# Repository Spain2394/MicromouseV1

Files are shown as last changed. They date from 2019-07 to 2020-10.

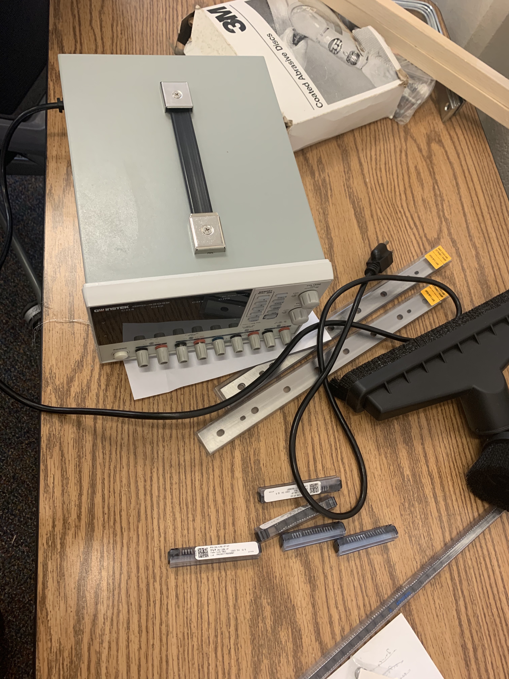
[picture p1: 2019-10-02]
docs/Notes/Electronics Notes/powersupplyy-return.jpg

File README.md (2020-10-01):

# Introduction
Micromouse (small robot car) PCB, boards are  designed in [EAGLE](http://eagle.autodesk.com)

Current board release [micromouse_board_revB_V0.0.16_2020-02-19.zip ](https://github.com/uga-robotics/MicromouseV1/blob/master/micromouse-main-board/micromouse-revB/micromouse_board_revB_V0.0.16_2020-02-19.zip ). Inside this zip file you will CAM files for assembly and manufacturing. 
Board BOM  --> [micromouse_board_revB_V0.0.16_2020-02-19.xlsx](https://github.com/uga-robotics/MicromouseV1/blob/master/micromouse-main-board/micromouse-revB/micromouse_board_revB_V0.0.16.xlsx)

## Getting going
Clone to hardware of software to local machine: ```git clone --recurse-submodules https://github.com/uga-robotics/MicromouseV1.git```

# Table of contents
1. [Bill Of Materials](https://github.com/Spain2394/MicromouseV1/blob/master/Wiki/Bill-of-Materials.md)
2. [Hardware Setup](https://github.com/Spain2394/MicromouseV1/blob/master/Wiki/Hardware-Setup.md)
3. [Software Setup](https://github.com/Spain2394/MicromouseV1/blob/master/Wiki/Software-Setup.md)

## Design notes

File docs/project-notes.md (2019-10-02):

# Project Notes:
### Resources
- [Futura robot information](http://micromouseusa.com/?page_id=1342)
- [Micromouse educational slides](http://micromouseusa.com/?page_id=1342)
- [Design Template: IEEE Micromouse Green Giant](http://greenye.net/Pages/Micromouse/Micromouse2012-2013.htm)
- [Design Template by: etank7000/Micromouse](https://github.com/etank7000/Micromouse)
- [Choosing IR Sensors](http://www.micromouseonline.com/2015/11/03/zeetah-sensor-design/)
- [Choosing a Motor](http://www.micromouseonline.com/2015/11/03/zeetah-sensor-design/)

### For Micromouse presentation slides see UCLA [notes](http://micromouse.ieeebruins.org/index.php/Main_Pages)

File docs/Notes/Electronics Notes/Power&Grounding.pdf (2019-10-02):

POWER AND GROUNDING

Dennis M. Briggs

Continuing Lecturer, UCLA Department of Electrical Engineering

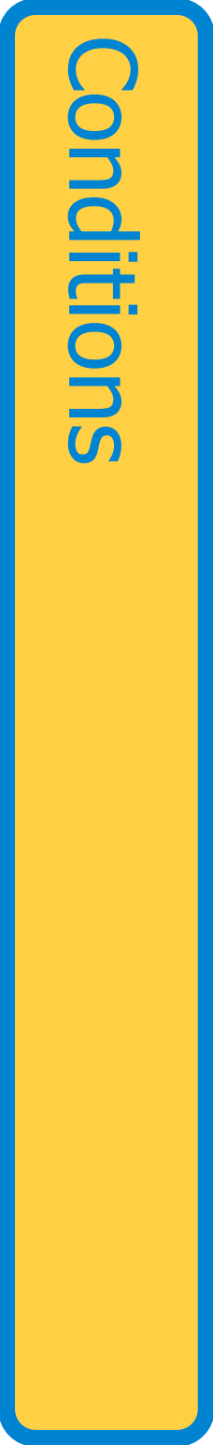
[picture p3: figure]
Conditions

- You will have one battery (OK, 2 for 7.4V)
- But you need different voltages
- + 5V0 for sensors
- +3V3 for microcontroller
- ± 5-7 V to drive motor control MOSFETS
- DC-to-DC converters can do these things

●
You will have one battery (OK, 2 for 7.4V)
- But you need different voltages
- + 5V0 for sensors
- +3V3 for microcontroller
- ± 5-7 V to drive motor control MOSFETS
- DC-to-DC converters can do these things

●
Charge Pumps
- High voltage, low current
- OK for driving MOSFETs
- Linear Regulators
- Simple
- Low noise
- Not efficient if big drop
- Standard andLow Dropout (LDO)
- Switching Regulators
- Efficient
- High noise
- Non-inverting & inverting
- Boost, Buck,and Buck-Boost

●
Charge Pumps
- High voltage, low current
- OK for driving MOSFETs
- Linear Regulators
- Simple
- Low noise
- Not efficient if big drop
- Standard andLow Dropout (LDO)
- Switching Regulators
- Efficient
- High noise
- Non-inverting & inverting
- Boost, Buck,and Buck-Boost

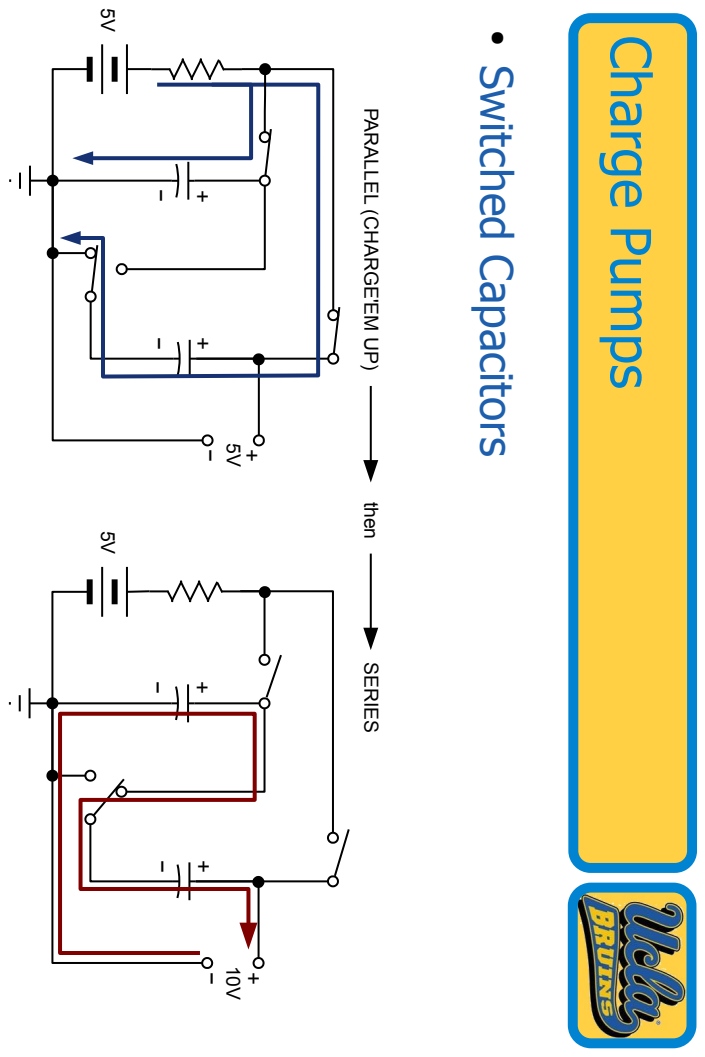
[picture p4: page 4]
● Switched Capacitors; Charge Pumps; then

PARALLEL (CHARGE'EM UP) SERIES

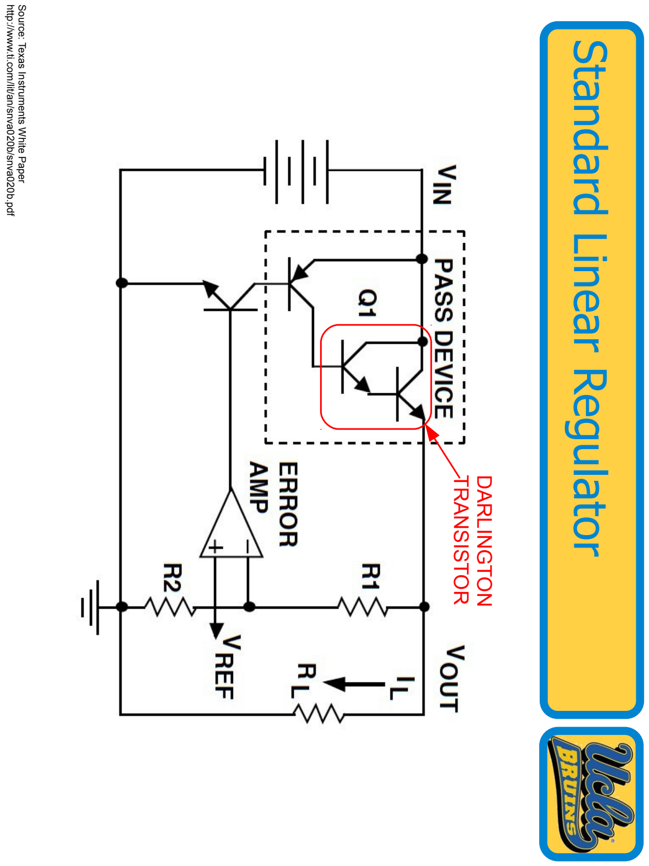
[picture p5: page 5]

Standard Linear Regulator

http://www.ti.com/lit/an/snva020b/snva020b.pdf

Source: Texas Instruments White Paper

TRANSISTOR

DARLINGTON

Standard Linear Regulator

http://www.ti.com/lit/an/snva020b/snva020b.pdf

Source: Texas Instruments White Paper

TRANSISTOR

DARLINGTON

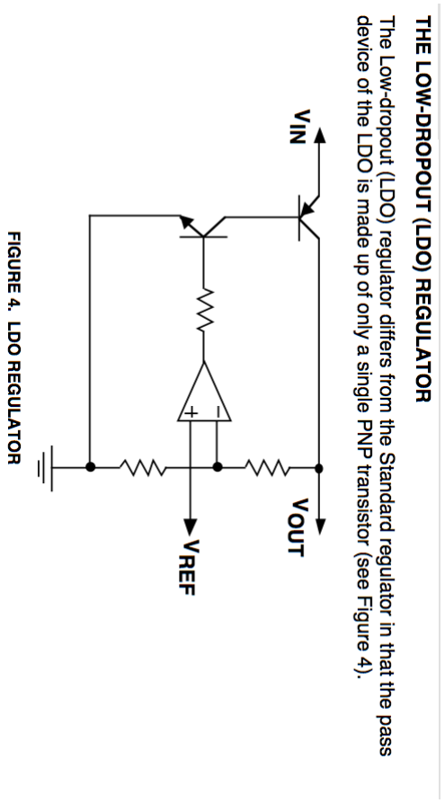
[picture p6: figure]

http://www.ti.com/lit/an/snva020b/snva020b.pdf

Source: Texas Instruments White Paper

v

n =

V REF

=

V OUT R2

R1

R2 V OUT

=
V REF

R1

R2

R2

=
V REF 1

R1

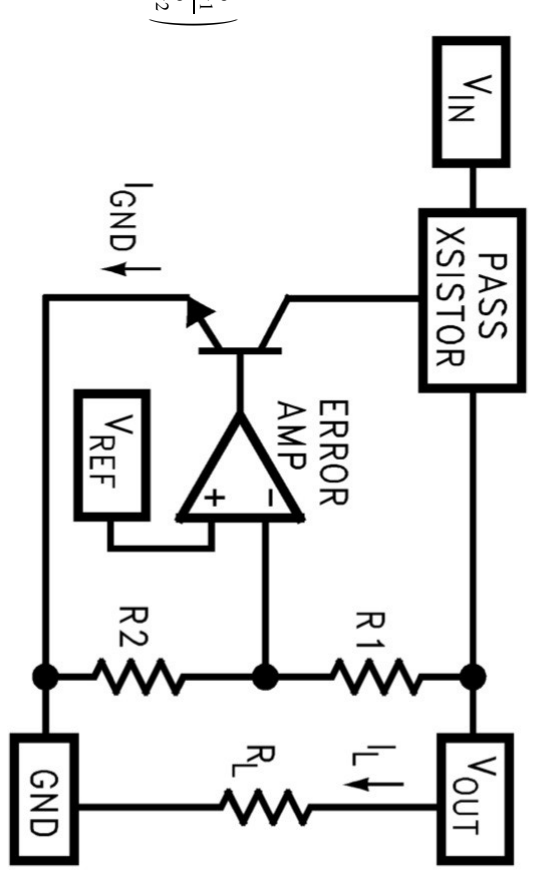
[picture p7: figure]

R2

holds.

summing point constraint

Negative feedback;

http://www.ti.com/lit/an/snva020b/snva020b.pdf

Source: Texas Instruments White Paper

v

n =

V REF

=

V OUT R2

R1

R2 V OUT

=
V REF

R1

R2

R2

=
V REF 1

R1

R2

holds.

summing point constraint

Negative feedback;

http://www.ti.com/lit/an/snva020b/snva020b.pdf

Source: Texas Instruments White Paper

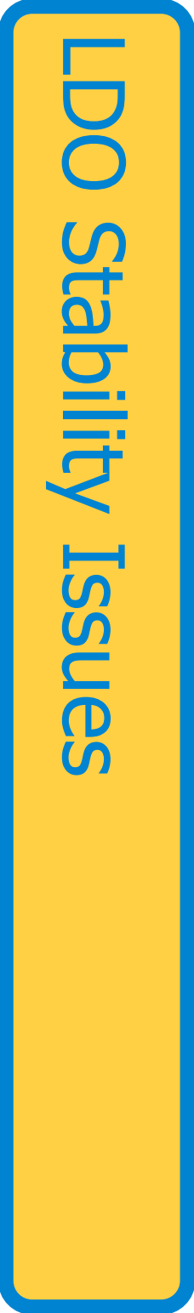
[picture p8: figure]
LDO Stability Issues

source: http://www.ti.com/lit/an/snva020b/snva020b.pdf

Source: Micrel MIC39000/39001/39002 Data sheet Source: Micrel MIC39000/39001/39002 Data sheet

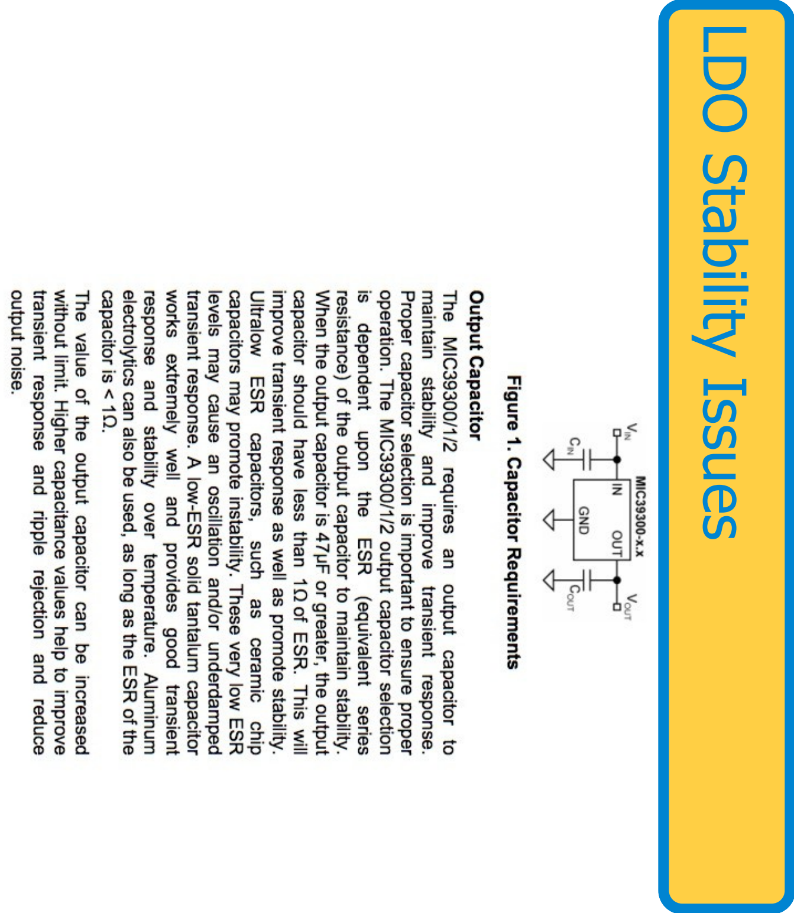
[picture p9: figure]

Stability Issues LDO Stability Issues Stability Issues LDO Stability Issues

http://www.national.com/assets/en/appnotes/f4.pdf

Source: National Semiconductor White Paper

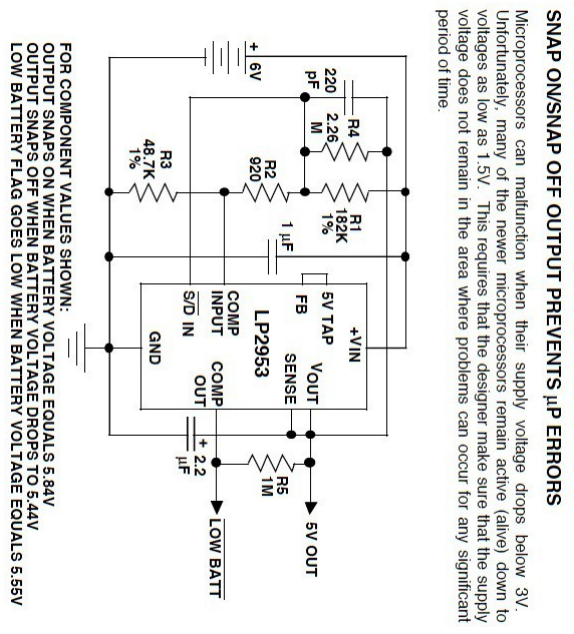
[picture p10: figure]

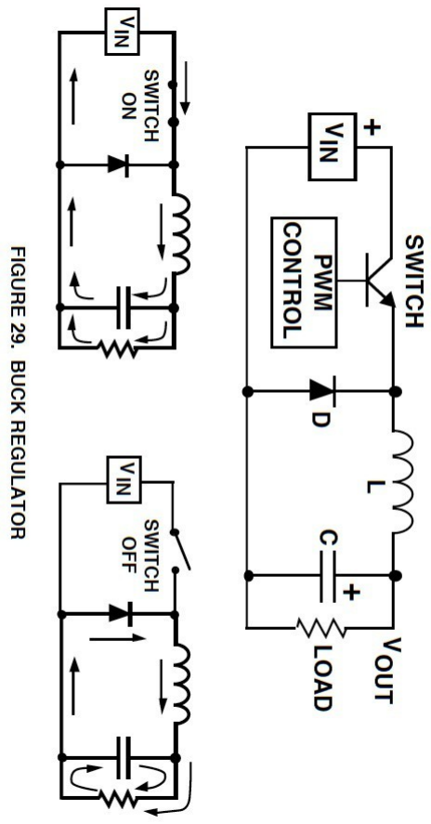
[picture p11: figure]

http://www.national.com/assets/en/appnotes/f5.pdf

Source: National Semiconductor White Paper

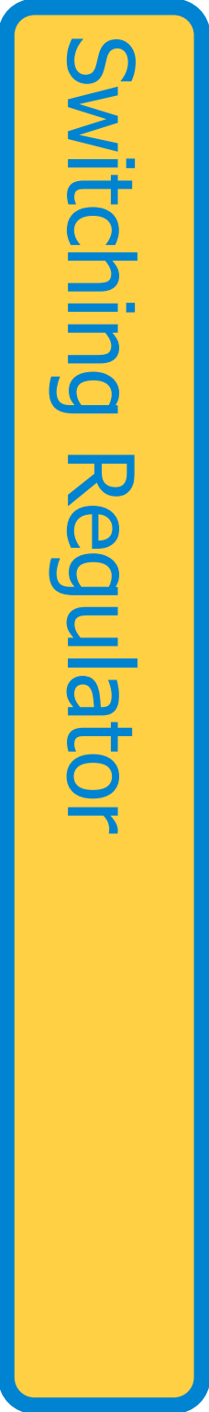
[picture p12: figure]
Switching Regulator

Source: Maxim Appnotes

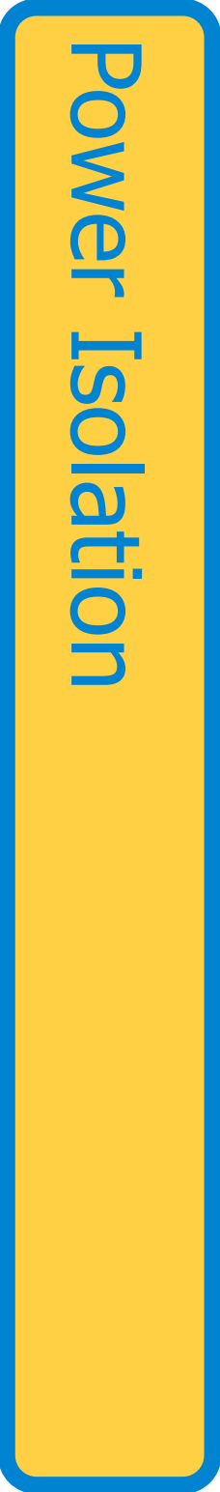
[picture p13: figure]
Power Isolation

Source: Prof. Richard Spencer, UCD

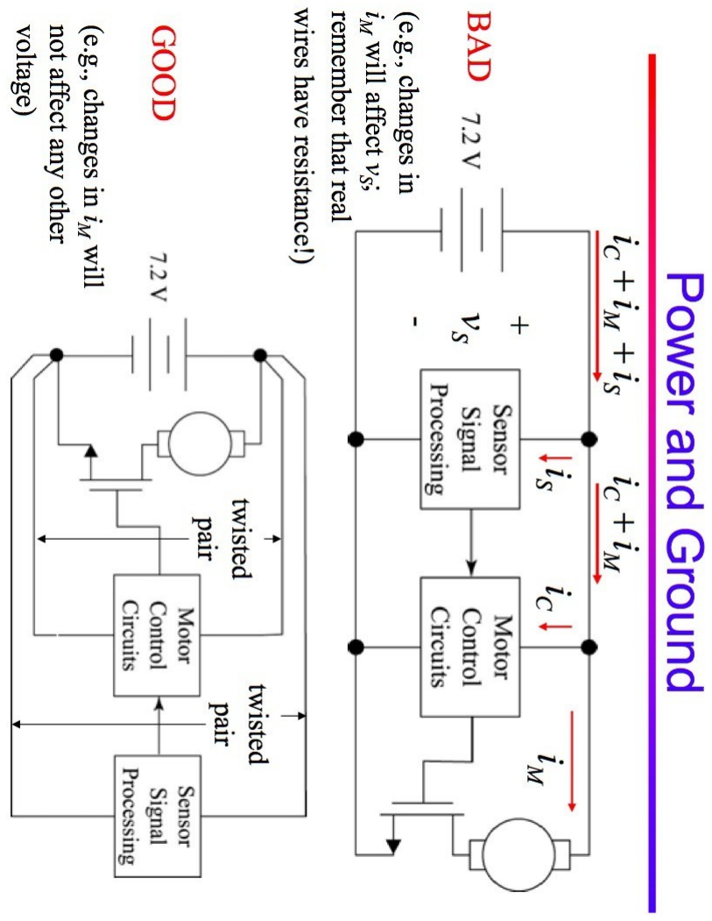
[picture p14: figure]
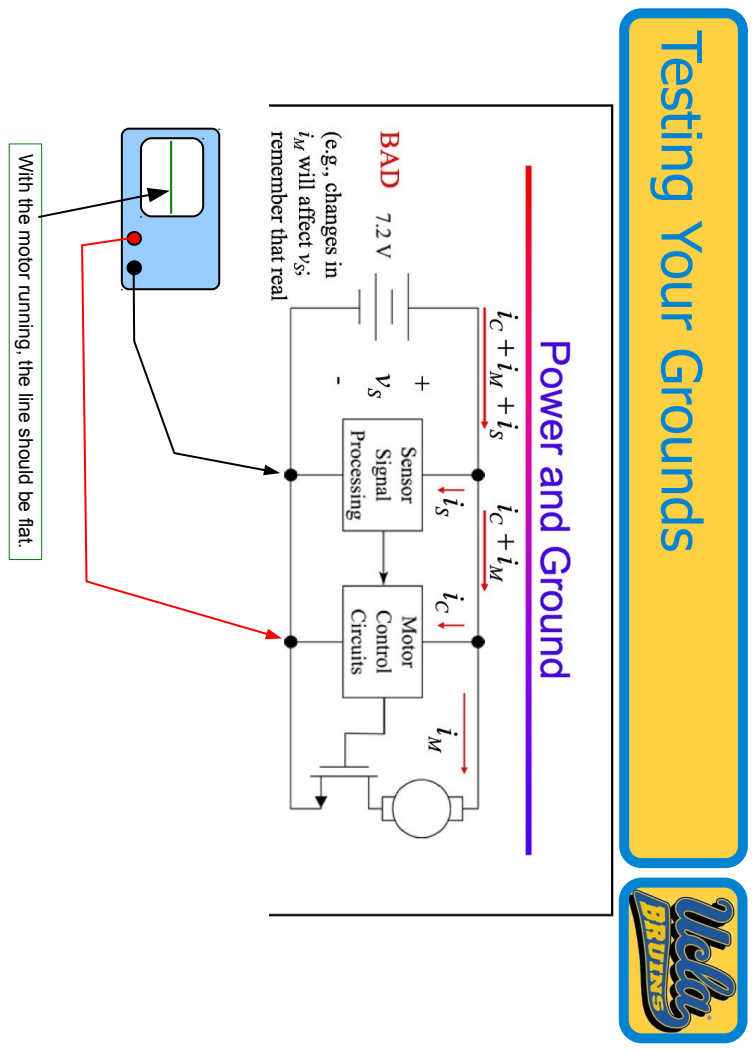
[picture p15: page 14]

Testing Your Grounds

With the motor running, the line should be flat.

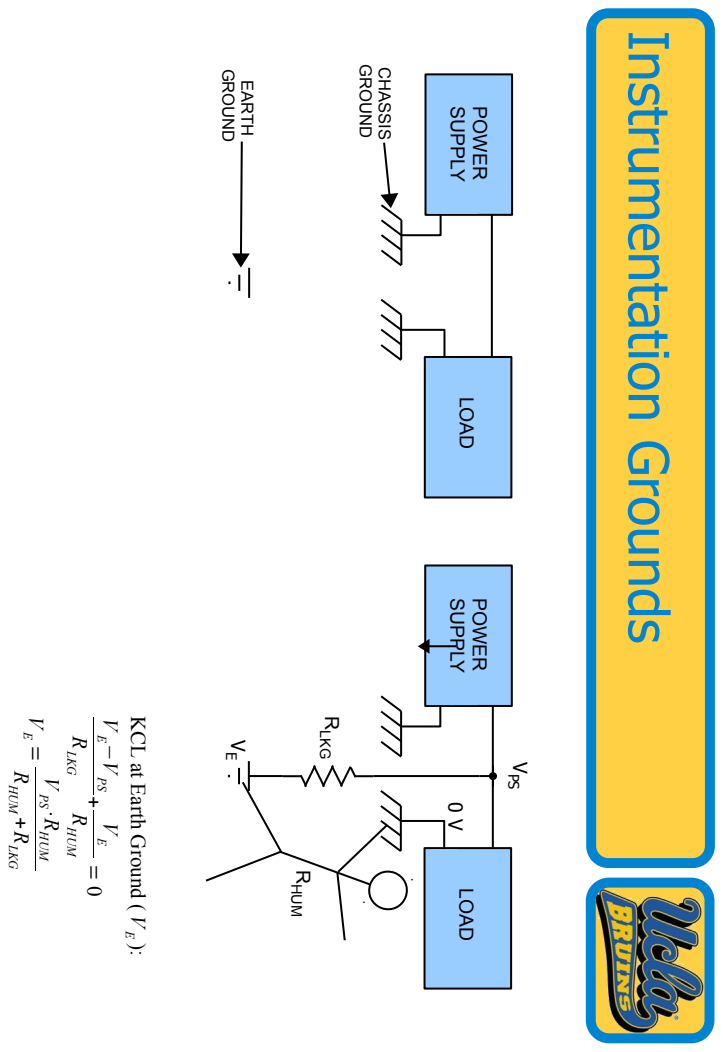
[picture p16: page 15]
Instrumentation Grounds; SUPPLY; GROUND; CHASSIS; EARTH; RLKG; RHUM; E − VPS; E = V PS⋅RHUM; + RLKG; VPS

POWER LOAD SUPPLY POWER LOAD

KCL at Earth Ground (

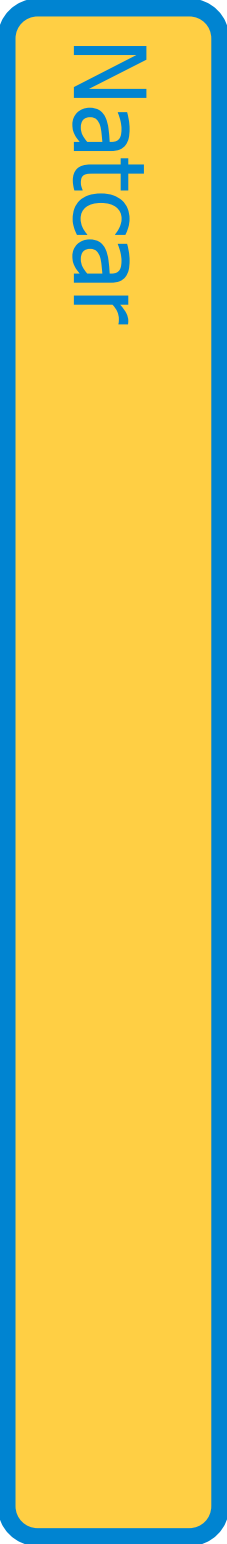
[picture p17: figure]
Natcar

A NATCAR GROUNDING STORY

Source: “NATCAR – Team Pathfinder”; John J. Jang, Siu Ching (Connie) Kwan, Sonny T. Bui, Michael

Chan, UCLA Department of Electrical Engineering, Final Report, Course EE184D, 2012-13 School Year

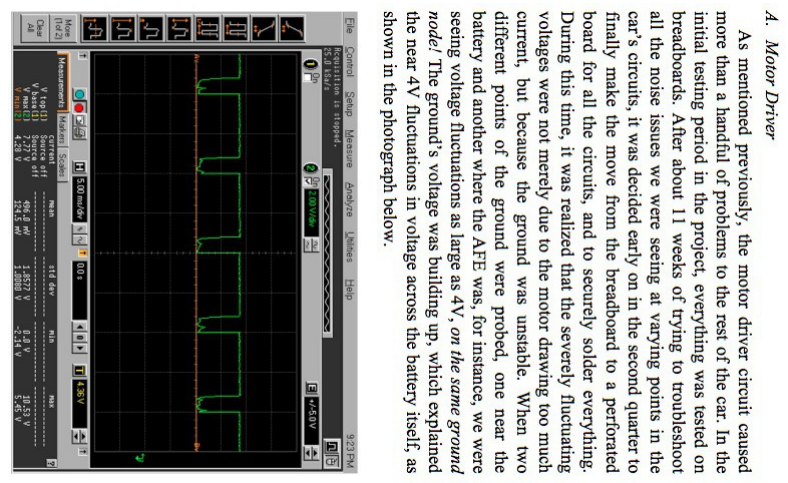
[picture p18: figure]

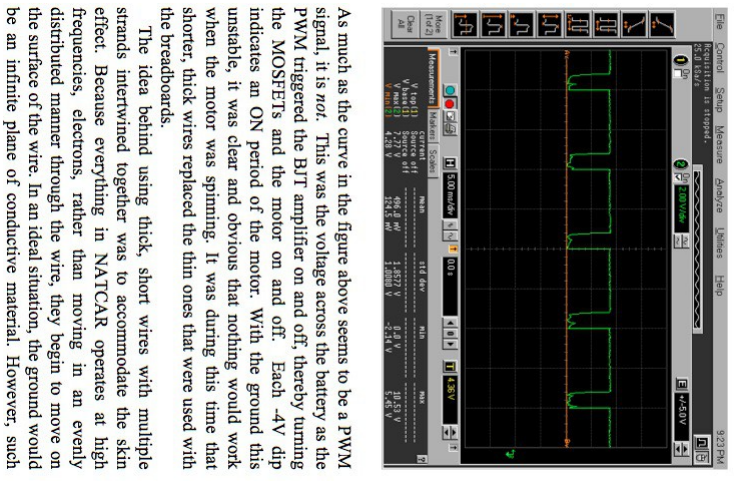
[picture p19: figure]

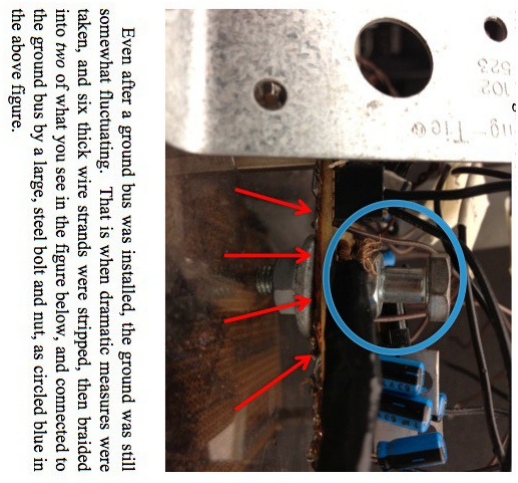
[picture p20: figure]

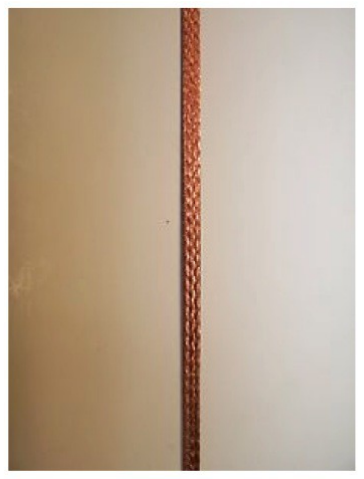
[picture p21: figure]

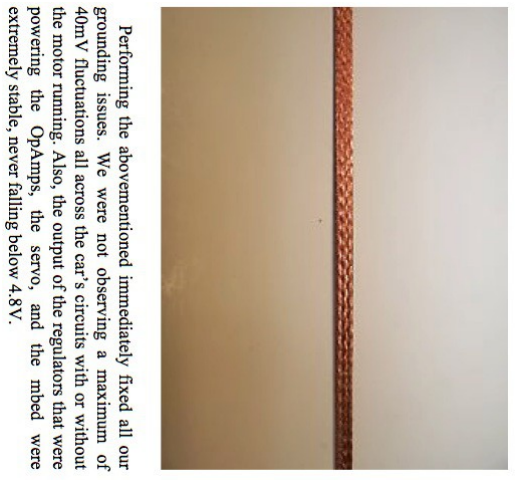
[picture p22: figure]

Power Isolation

Source: Prof. Richard Spencer, UCD

1/4-20 BOLT

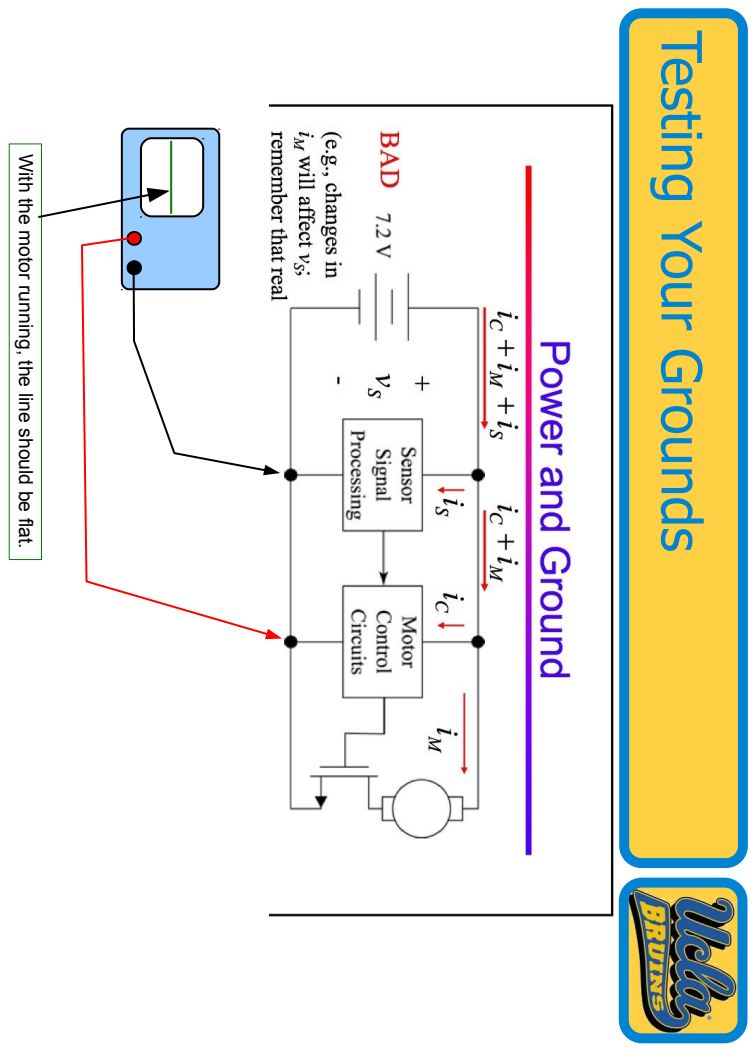
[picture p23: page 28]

Testing Your Grounds

With the motor running, the line should be flat.

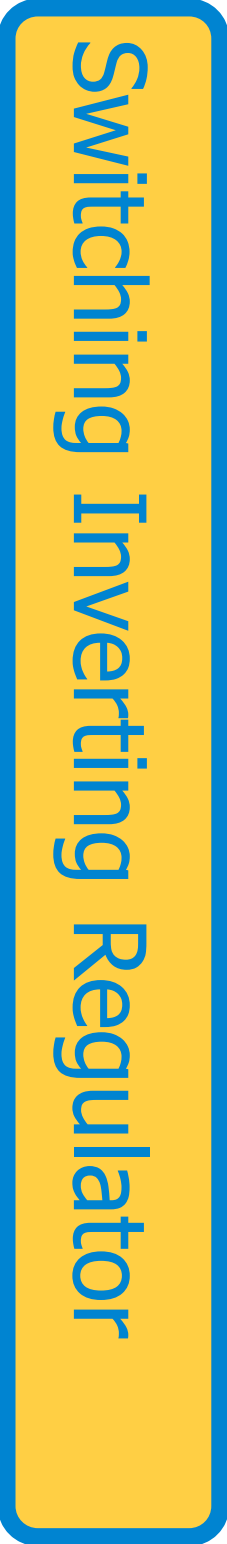
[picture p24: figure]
Switching Inverting Regulator

http://www.national.com/assets/en/appnotes/f5.pdf

Source: National Semiconductor White Paper

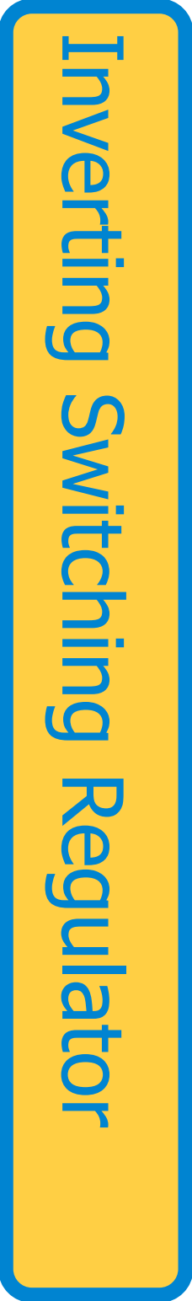
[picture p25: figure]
Inverting Switching Regulator

Source: Prof. Richard Spencer, UCD

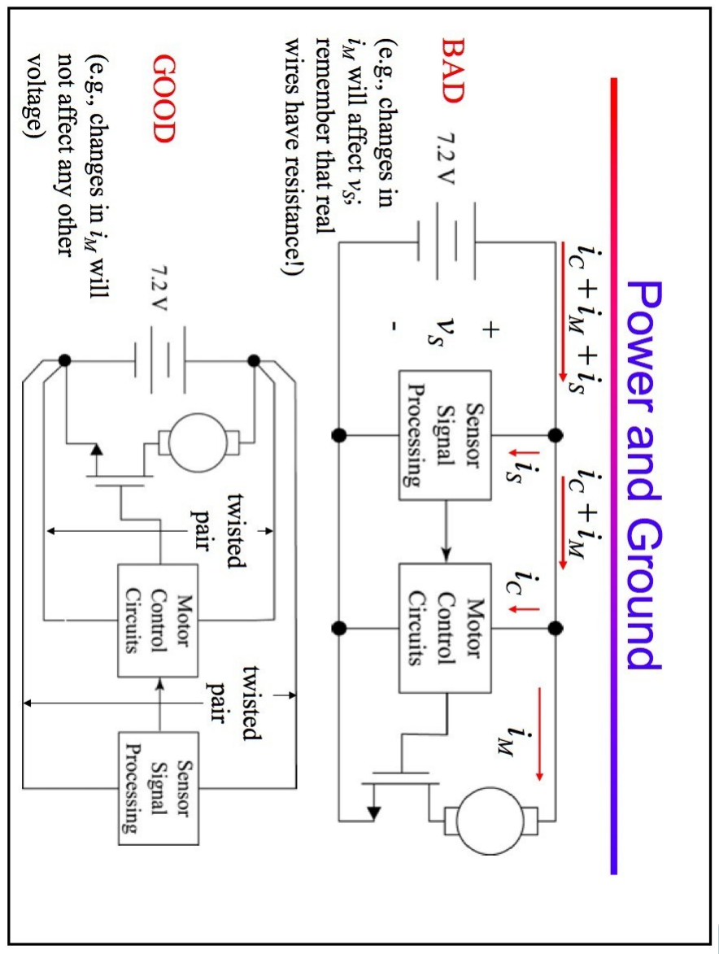
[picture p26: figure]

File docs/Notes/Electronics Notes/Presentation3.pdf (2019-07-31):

MicroMouse: Motors, Encoders, and Power, Oh my

Saturday, November 10, 12

Motors and Encoders

## Types of Motors


- DC
- BLDC
- Materials
- Graphite
- Metallic

## Motor properties

- Power requirements
- Nominal voltage
- Stall current
- Gear ratio
- Maximum RPM
- Dimensions

## Controlling your motor


- Speed proportional to voltage
- H-Bridge
- Allows forward and reverse drive
- PWM
- Approximation of analog output
- Maximize applied voltage with MOSFET


## What is an encoder?

- Let’s you figure how far you’ve gone
- Measures angular displacement
- Translates to distance traveled
- Can also be used for feedback control

## Encoder properties

- Resolution
- Ticks per revolution


- Methods of measurement
- Optical
- Magnetic
- Power requirements


## Encoder Logic

- Most use quadrature encoding
- Grey code for those of you in EE M16
- Magnetic use Hall Effect sensor
- Optical use IR sensors
B leads A (forward) | A leads B (backward)

Power System

## Basic Components


- Battery
- Voltage regulators
- Filtering capacitors


## Power Distribution

- Power-hungry parts
- Motor system: ~500mA per motor
- IR Sensors: ~40mA per sensor
- Low-power parts
- MCU: ~30mA
- Other sensors
- Gyro and encoders: <10mA total

## Voltage Regulators

- Different voltages for different components
- 3.3v and 5v


- Very inefficient, but easy to configure
- Suitable for our purposes

## Filtering Capacitors

- Especially useful for sensors
- Connect between power and ground
- Smooth voltage ripple
- Give ground path for high frequency noise
- Lower capacitance = Higher cutoff frequency
- Values around 10uF and 0.1uF work well

## Recommended Batteries

- Li-Po’s are the best!
- Small
- High power density
- Or maybe not


- Require specific charging profile
- Don’t stab them!!!

Some Recommended Choices

## Motors and Encoders

- GM9 Motors from Pololu
- Matched with Wheel Watcher Kit
- Pololu motor and encoder kit
- Metal gearbox
- Faulhaber Motors
- Super high performance
- Only for high budget

## Choosing Parts

- Create spreadsheet from our template
- Share with us
- Add microcontroller and motor choices
- Including vendor, part no., and other information
- This will be how you order parts

## Next Meeting’s Agenda


Sensors!!!


## Deposits

- We’ll call you up by team
- Make checks out to UCLA IEEE
- If you don’t have it now, drop it off in the IEEE Lab before next Thursday!

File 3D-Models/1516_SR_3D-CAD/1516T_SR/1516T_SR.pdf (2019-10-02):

Wenn Sie diesen Text sehen, stellen Sie bitte

"Kommentare und Fomulare" im Drucken Dialog

auf "Dokument und Markierungen"

Explosion / Teile bewegen

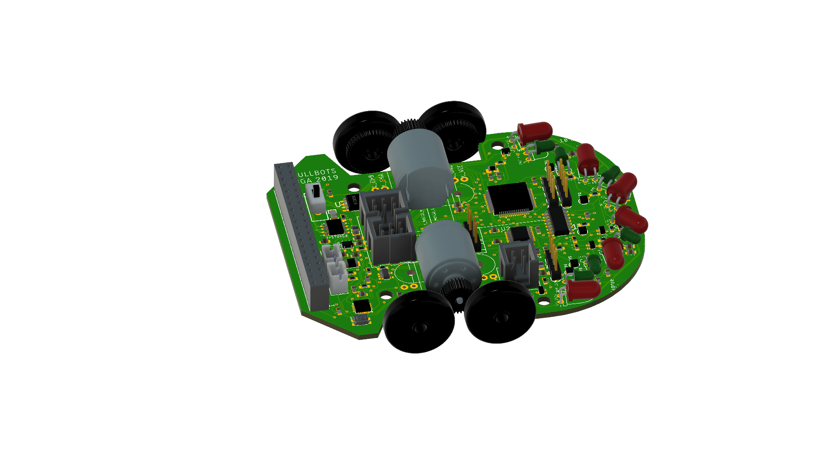
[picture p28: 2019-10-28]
3D-Models/Images/MicromouseV1.0.0v7-smooth.png

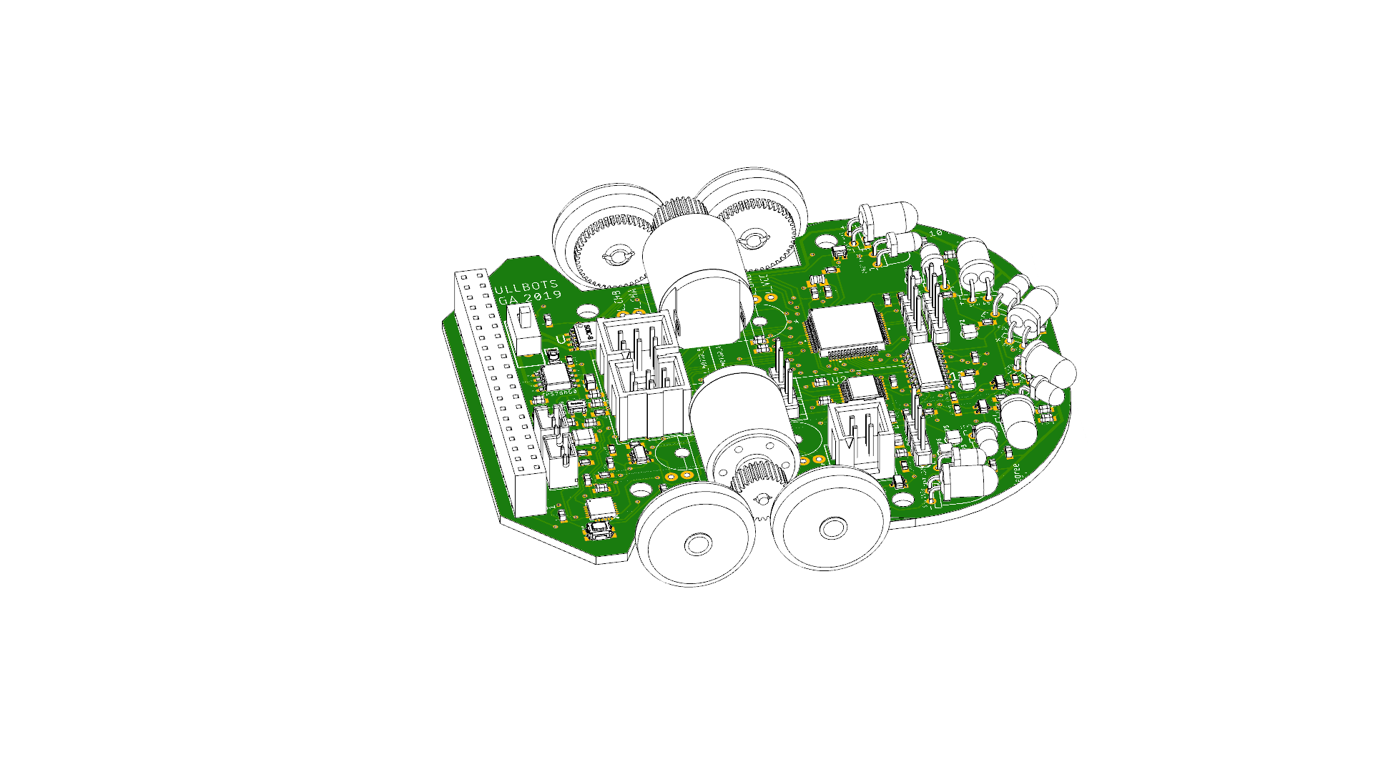
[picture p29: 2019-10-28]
3D-Models/Images/micromouse-edu-1.0.0-grey.png

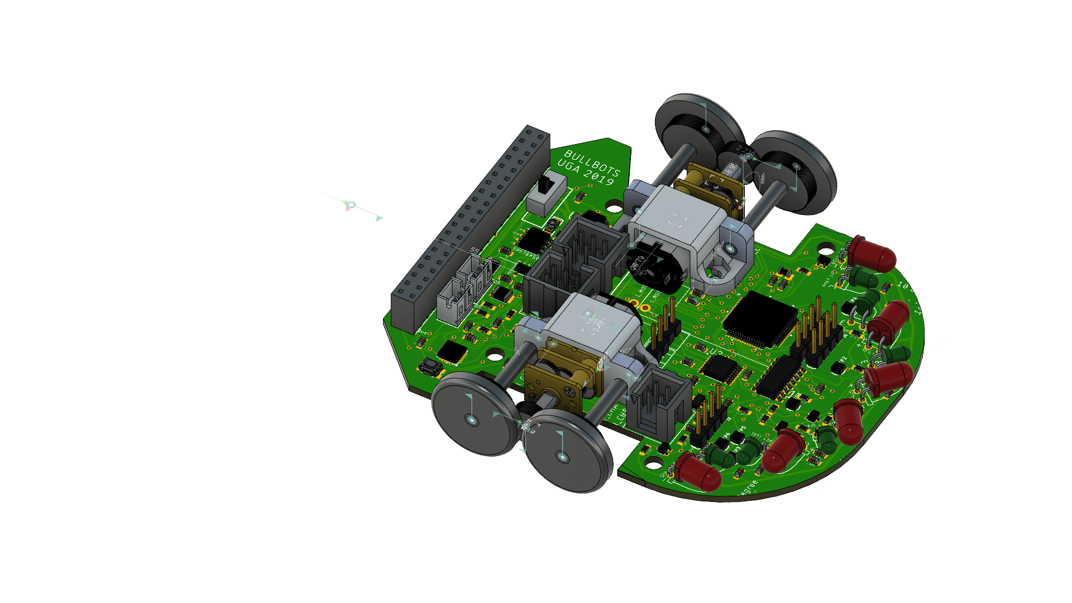
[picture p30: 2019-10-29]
3D-Models/Images/micromouse-edu-1.0.0 v1.png

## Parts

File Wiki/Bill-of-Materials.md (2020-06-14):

# Bill of Materials :electron:

This page will list everything you will need to design a micromouse. This design is based on the [Green Giant](http://greenye.net/Pages/Micromouse/Micromouse2016-2017.htm).

## Primary Parts
You need these components to enable the micromouse to sense its environment and

| Part | Qty | Cost  |URL |
| --- |:---:| -----:|:---:|
| Microcontroller | 1 | $8.69 | [Arrow](https://www.arrow.com/en/products/stm32f103ret6/stmicroelectronics)|
| Accererometer/Gyroscope |1 | $12.45  |[Digikey](https://www.digikey.com/product-detail/en/tdk-invensense/MPU-6000/1428-1005-1-ND/4038alt-cmd-t006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)|
|Motor Driver (H-Bridge) |1 | $2.51 |[Digikey](http://www.ti.com/lit/ds/symlink/drv8848.pdf)|
|Battery | 2 | $4.99|[eBay](https://www.ebay.com/itm/3-7V-110-mAh-401230-LiPo-Polymer-Battery-Rechargeable-for-GPS-Bluetooth-041230/263809499945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)|
| IR Emitter | 6 | $ 4.62| [Digikey](https://www.digikey.com/product-detail/en/osram-opto-semiconductors-inc/SFH-4545/475-2919-ND/2205955)|
| IR Reciever |  6 |  $4.26  |[Digikey](https://www.digikey.com/product-detail/en/vishay-semiconductor-opto-division/TEFT4300/751-1041-ND/1681175)|
| PCB Boards |  10| $18.81|[JLCPCB](https://jlcpcb.com)|
|  Encoder (IE2 – 1024) + Motor (1516T006SR) |4 | $122.90 |Faulhaber [1](https://www.faulhaber.com/en/products/series/ie2-1024/),[2](https://www.faulhaber.com/fileadmin/Import/Media/EN_IE2-1024_DFF.pdf)|
| Tires| 1 | $9.51| [eBay](https://www.ebay.com/itm/Kyosho-Mini-Z-MZW2-20-High-Grip-Tire-Set-20/302534111257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)|
| Wheels | 1 | $2.99 | [ReFlexRacing](http://www.reflexracing.net/Atomic-Mini-Z-AWD-Narrow-Split-Spoke-Wheels-0-offset-black_p_614.html)|

## Optional/Testing Parts
| Part | Qty | Cost |URL |
| --- |:---:| -----:|:---:|
| Blue Pill (SMT developer)| 1|$18.99|[Amazon](https://www.amazon.com/initeq-STM32F103C8T6-Minimum-Development-Programmer/dp/B079B95L9Y) |
| Gear Set | 1| $12.20| [eBay](https://www.ebay.com/itm/Kyosho-Mini-Z-MD006-Pinion-Spur-Gear-Set-Mini-Z-AWD/283310653492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)|
| MPU 6050 |1 | $4.80|[Amazon](https://www.amazon.com/dp/B07DXQB6P1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)|
| Incremental Encoder|1|$8.99|[Amazon](https://www.amazon.com/Cylewet-Encoder-15×16-5-Arduino-CYT1062/dp/B06XQTHDRR/ref=as_li_ss_tl?s=electronics&ie=UTF8&qid=1519833881&sr=1-3&keywords=Rotary+Encoder&linkCode=sl1&tag=howto045-20&linkId=8342c1bffd186172203db659d13e7449)|

### Next
Go to [hardware setup](https://github.com/Spain2394/MicromouseV1/blob/master/Wiki/Hardware-Setup.md)

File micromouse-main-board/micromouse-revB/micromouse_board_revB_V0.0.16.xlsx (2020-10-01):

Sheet: Micromouse-BOM
Part | Value | Package | Description | Availability | Pn | Unit Cost | Mfn | Qty | Price | Comments | On Board | Notes | Notes
C10 | 10 nF | 0603-cap | capacitor | available | 1276-1028-1-ND | $0.10 | Samsung Electro-Mechanics | 1 | $0.10 | IN
C1 | 1.0uF | 0603-cap | capacitor | available | 1276-1013-1-ND | $0.10 | Samsung Electro-Mechanics | 1 | $0.10 | IN |  | Wrong size
C2,C8,C18,C21,C23,C_ELF1,C_EM_D1,C_ERF1,C_E_H1 | 4.7uF | 0603-cap | capacitor | available | TMK107BBJ475MA-T | $0.31 | Taiyo Yuden | 9 | $2.79 | IN | !C18, !C23 | C_ERF1 placed
C3 | 1.4 uF | 0603-cap | capacitor | available | C1812C145J5JLC7805 | $6.69 | KEMET | 1 | $6.69 | IN
C13 | 1nF | 0603-cap | capacitor | available | CL10B102KB8NNNC (https://www.digikey.com/product-detail/en/samsung-electro-mechanics/CL10B102KB8NNNC/1276-1018-1-ND/3889104) | $0.10 | Samsung Electro-Mechanics | 1 | $0.10 | IN | placed
C5,C6,C7,C12,C17,C22,C_3.3V2,C_5V1,C_BAT1,C_ELF2,C_EM_D2,C_ERF2,C_E_H2,C_GY_REG,C_GY_VDD,C_NR,C4 | 0.1uF | 0603-cap | capacitor | available | LMF107B7104KAHT | $0.27 | Taiyo Yuden | 16 | $4.32 | IN | !C7, !C17 | C_ERF2 placed
C9,C16 | 2.2uF | 0603-cap | capacitor | available | LMK107B7225MA-TR | $0.32 | Taiyo Yuden | 2 | $0.64 | IN |  | Need to place C16, and Test C9 | C16 placed, still need to test C9 with fluke 287
C15,C_3.3V1 | 10uF | 0603-cap | capacitor | available | C0603C106M8PACTU | $0.56 | KEMET | 2 | $1.12 | IN (Bag has a different part number) | placed
C20 | 1000pF | 0603-cap | capacitor | available | C0603C102K4RECAUTO | $0.15 | KEMET | 1 | $0.15 | IN | placed
CR1 | STM32F103RET6 | lqfp-64 | arm cortex m3 mcu | available | STM32F103RET6 | $7.95 | STMicroelectronics | 1 | $7.95 | IN | placed
C_5V2,C_BAT2 | 47uF | cap 0805-cap | capacitor | available | CL31A476MQHNNWE (https://www.digikey.com/product-detail/en/samsung-electro-mechanics/CL31A476MQHNNWE/1276-3064-1-ND/3891150) | $0.46 | Samsung Electro-Mechanics | 2 | $0.92 | IN | placed
C_GY_CP | 2.2nF | 0603-cap | capacitor | available | C0603C222K5RACTU (https://www.digikey.com/product-detail/en/kemet/C0603C222K5RACTU/399-1085-1-ND/411360) | $0.10 | KEMET | 1 | $0.10 | IN | placed
D1 | - | sot23 | z-diode | available | BZX84B12VLFHT116 (https://www.mouser.com/ProductDetail/ROHM-Semiconductor/BZX84B12VLFHT116) | $0.22 | ROHM Semiconductor | 1 | $0.22 | IN | placed
IC1 | LM321MFX | sot23-5 | low power single op amp | available | LM321MFX/NOPB | $0.65 | Texas Instruments | 1 | $0.65 | IN | Placed
J1,J2,J4 | - | 1x04 | multi connection point. often used as generic header-pin footprint for 0.1 inch spaced/style header connections | available | 732-5317-ND (https://www.digikey.com.mx/product-detail/en/wurth-electronics-inc/61300411121/732-5317-ND/4846827) | $0.18 | Wurth Electronics Inc. | 3 | $0.54 | IN
J3,J5 | HTSS-103-XX-XX-D | htss-103-xx-xx-d | - | available | HTSS-103-01-G-D (https://www.samtec.com/products/htss-103-01-g-d) | $1.82 | Samtec | 2 | $3.64
J6,J7 | HTSS-102-XX-XX-D | htss-102-xx-xx-d | breakout header | - | DNC | - | - | 2 | - | - | -
JP1,JP3 |  | molex-1x2 | header 2 | available | 732-5315-ND | $0.13 | Wurth Electronics Inc. | 2 | $0.26 | IN
L1 | 10uH | 1007 | inductors | available | LB2518T221K | $0.16 | Taiyo Yuden | 1 | $0.16 | IN | Placed
LED_PWR | green | led-1206 | leds | available | APT3216ZGC | $0.58 | Kingbright | 1 | $0.58 | IN | Placed | Need to place LED_PWR
NMOS1,NMOS2,NMOS3,NMOS4 | DMN3150LW | dmn3150lw | - | available | DMN3150LW-7 |  | Diodes Incorporated | 4 | $0.00 | IN | placed
R1 | 1k | m0805 | resistor | available | PNM0805E1001JBT0 | $6.81 | Vishay / Thin Film | 1 | $6.81 | IN | placed
R2 | 10k | 805 | resistor | available | RC0805FR-0710KL | $0.10 | Yageo | 1 | $0.10 | IN | placed
R3 | 1k | r0805 | resistor | available | RN73R2ATTD1001D25 | $0.39 | KOA Speer | 1 | $0.39 | IN | placed
R8,R9 | 500m | 805 | resistor | available | RC0805FR-07100RL | $0.10 | Yageo | 2 | $0.20 | Missing part
R_ED1,R_ED2,R_EH1,R_EH2 | 5.6 | 0603-res | resistor | available | P5.6BZDKR-ND | $0.11 | Panasonic Electronic Components | 4 | $0.44 | IN | placed, missing R_ED2 |  | Placed
R_ED_PD,R_EH_PD,R_ELF_PD,R_ERF_PD | 47k | 0603-res | resistor | available | 541-47.0KSCT-ND | $0.18 | Vishay Dale | 4 | $0.72 | IN | placed
R_ELF,R_ERF | 10 | 0603-res | resistor | available | 541-10.0SDKR-ND | $0.28 | Vishay Dale | 2 | $0.56 | IN
R_PWR,R_VM7 | 1k | 0603-res | resistor | available | 541-1.00KSCT-ND | $0.28 | Vishay Dale | 2 | $0.56 | IN
R_RLD,R_RLF,R_RLH,R_RRD,R_RRF,R_RRH | 1.8k | 0603-res | resistor | available | RHM1.8KDCT-ND | $0.10 | Rohm Semiconductor | 6 | $0.60 | IN | !R_RRF,!R_RRH
R_VM1 | 75k | 0603-res | resistor | available | RHM75KDCT-ND | $0.10 | Rohm Semiconductor | 1 | $0.10 | IN | placed
R_VM2 | 33k | 0603-res | resistor | available | P33KBZDKR-ND | $0.11 | Panasonic Electronic Components | 1 | $0.11 | IN | placed
R_VM4, R_VM5 | 100k | 0603-res | resistor | available | RHM100KADCT-ND | $0.13 | Rohm Semiconductor | 2 | $0.26 | IN | placed
R_VM6 | 3.3k | 0603-res | resistor | available | P3.3KBYDKR-ND | $0.16 | Panasonic Electronic Components | 1 | $0.16 | IN
S1 | RESET | tactile_switch_smd_4.6x2.8mm | various no switches- pushbuttons | available | 611-KMR431GULCLFS (https://www.mouser.com/ProductDetail/CK/KMR431GULCLFS) | $0.29 | C&K | 1 | $0.29 | IN
S2 |  | switch-spdt | spst switch | available | COM-00102 | $1.50 | Sparkfun | 1 | $1.50 | IN
U$1,U$2 | JST_CONNECTOR_FEMALE | jst_connector_female | - | available | 455-1611-ND | $0.14 | JST Sales America Inc. | 1 | $0.14 | IN
U$3 | TPS73633(SOT-23) | tps73633(sot-23) | - | available | TPS73633MDBVREPG4 | $5.85 | Texas Instruments | 1 | $5.85 | IN | placed
U$4 | TPS76850(SOIC-8) | tps76850(soic-8) | - | available | TPS76850QDR | $2.78 | Texas Instruments | 1 | $2.78 | IN | placed
U$12 | MY_MM_MOTOR_MOUNT | my_mm_motor_mount | - | DNC | DNC | DNC | DNC | 1 |  | 2 motors will be purchased seperately
U1 | SN74HC151DR | soic127p600x175-16n | 8-line to 1-line dataselectors /multiplexers | available | 296-14834-1-ND | $0.51 | Texas Instruments | 1 | $0.51 | IN | placed
U2 | DRV8848PWPR | sop65p640x120-17n | none | available | 296-47770-1-ND | $1.53 | Texas Instruments | 1 | $1.53 | IN | placed
U3 | ACS712 | soic127p600x175-8n | PWM | available | 620-1190-1-ND | $4.34 | Allegro MicroSystems, LLC | 1 | $4.34 | IN | placed
U6 | MPU-6000 | qfn-24-ep | invensense mpu-6000 6-axis gryoscope/accelerometer | available | 1428-1005-1-ND | $12.44 | TDK InvenSense | 1 | $12.44 | IN
X1 | RASPI_GPIO_B+#_PIN | raspi_gpio_b+_pin | 2x20 header connector | availble | 1992 | $2.95 | Adafruit | 1 | $2.95
E1,E2,E3,E4,E5,E6 | - | - | ir emitter | available | 475-2919-ND | $0.77 | OSRAM Opto Semiconductors Inc. | 6 | $4.62 | IN
REC_1,REC_2,REC_3,REC_4,REC_5,REC_6 | - | - | ir phototransistor | available | 751-1041-ND | $0.71 | Vishay Semiconductor Opto Division | 6 | $4.26 | IN
 |  |  |  |  |  |  |  | Total | $83.25
Total | $83.25

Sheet: Missing-Parts
Value | Value |  | Description | Availability | Unit Cost | Price | Mfn | Qty | Unit Price | Purchased
J3, J5 | HTSS-103-XX-XX-D | htss-103-xx-xx-d | - | available | HTSS-103-01-G-D (https://www.samtec.com/products/htss-103-01-g-d) | $1.82 | Samtec | 2 | $3.64 | Yes
R8, R9 | 500m Ohm | 805 | Resistor | available | CSR0805FKR500TR-ND | $0.10 | Digikey | 2 | $0.30 | Yes
X1 | RASPI_GPIO_B+#_PIN | raspi_gpio_b+_pin | 2x20 header connector | available | - | $2.95 |  | 1 | $2.95 | -
- | - | - | 10:1 Micro Metal Gearmotor HP 6V with Extended Motor Shaft | available | - | $16.95 | Polulo (https://www.pololu.com/product/2211) | 4 | $16.95 | Yes
C1 | 1.0uF | 0603-cap | capacitor | available | 1276-1182-1-ND | $0.10 | Samsung Electro-Mechanics | 10 | $1.00 | Yes

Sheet: Still-Need
Value | Value | Package | Description | Availability | Pn | Unit Cost | Mfn | Qty | Comments
- | Batteries |  | Yes | available |  | $3.39 | Amazon
C10 | 10 nF | 0603-cap | capacitor | available | 1276-1028-1-ND | $0.10 | Samsung Electro-Mechanics | 1
C1 | 1.0uF | 0603-cap | capacitor | available | 1276-1013-1-ND | $0.10 | Samsung Electro-Mechanics | 1
- | - | - | EBL 14500 Li ion Rechargeable Battery 3.7V 800mAh + Charger | available | - | $6.99 | Ebay | 1
 |  |  | Assorted Metric Hardware | available |  | $20.99 | Amazon (https://www.amazon.com/Washers-1200PCS-Sutemribor-Assortment-Wrenches/dp/B07H4MG7TC?s=industrial)

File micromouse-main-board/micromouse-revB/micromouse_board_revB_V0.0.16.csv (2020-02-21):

Part | Value | Device | Package | Description | AVAILABILITY | DESCRIPTION | DIGI-KEY_PART_NUMBER | DIGI-KEY_PURCHASE_URL | MANUFACTURER_PART_NUMBER | MF | MP | PACKAGE | PRICE | PROD_ID | SF_ID | SPICEPREFIX | VALUE | VENDOR
3.3V_PWR | green | LED1206 | LED-1206 | LEDs
5V_PWR | green | LED1206 | LED-1206 | LEDs
6V_PWR | green | LED1206 | LED-1206 | LEDs
B1 |  | TAC_SWITCHSMD | TACTILE-SWITCH-SMD | Momentary Switch |  |  |  |  |  |  |  |  |  | SWCH-08247 |  |  | TAC_SWITCHSMD
B2 |  | TAC_SWITCHSMD | TACTILE-SWITCH-SMD | Momentary Switch |  |  |  |  |  |  |  |  |  | SWCH-08247 |  |  | TAC_SWITCHSMD
B3 |  | TAC_SWITCHSMD | TACTILE-SWITCH-SMD | Momentary Switch |  |  |  |  |  |  |  |  |  | SWCH-08247 |  |  | TAC_SWITCHSMD
C1 | 10nF | CAP0603-CAP | 0603-CAP | Capacitor
C2 | 4.7uF | CAP0603-CAP | 0603-CAP | Capacitor
C4 | 0.1uF | CAP0603-CAP | 0603-CAP | Capacitor
C7 | 0.1uF | CAP0603-CAP | 0603-CAP | Capacitor
C8 | 1uF | CAP0603-CAP | 0603-CAP | Capacitor
C17 | 0.1uF | CAP0603-CAP | 0603-CAP | Capacitor
C18 | 4.7uF | CAP0603-CAP | 0603-CAP | Capacitor
C21 | 4.7uF | CAP0603-CAP | 0603-CAP | Capacitor
C22 | 0.1uF | CAP0603-CAP | 0603-CAP | Capacitor
C23 | 4.7uF | CAP0603-CAP | 0603-CAP | Capacitor
CR1 | STM32F103RET6 | STM32F103RET6 | LQFP-64 |  |  |  |  |  | STM32F103RET6 |  |  |  |  |  |  |  |  | STMicroelectronics
C_3.3V1 | 10uF | CAP0603-CAP | 0603-CAP | Capacitor
C_3.3V2 | 0.1uF | CAP0603-CAP | 0603-CAP | Capacitor
C_3.3V5 | 1uF | CAP0603-CAP | 0603-CAP | Capacitor
C_3.3V6 | 10uF | CAP0603-CAP | 0603-CAP | Capacitor
C_3.3V7 | 0.1uF | CAP0603-CAP | 0603-CAP | Capacitor
C_5V1 | 0.1uF | CAP0603-CAP | 0603-CAP | Capacitor
C_5V2 | 47uF | CAP1210 | 1210 | Capacitor
C_BAT1 | 0.1uF | CAP0603-CAP | 0603-CAP | Capacitor
C_BAT2 | 47uF | CAP1210 | 1210 | Capacitor
C_D | 0.1uF | CAP0603-CAP | 0603-CAP | Capacitor
C_D1 | 10uF | CAP0603-CAP | 0603-CAP | Capacitor
C_D2 | 2.2uF | CAP0603-CAP | 0603-CAP | Capacitor
C_ELF1 | 4.7uF | CAP0603-CAP | 0603-CAP | Capacitor
C_ELF2 | 0.1uF | CAP0603-CAP | 0603-CAP | Capacitor
C_EM_D1 | 4.7uF | CAP0603-CAP | 0603-CAP | Capacitor
C_EM_D2 | 0.1uF | CAP0603-CAP | 0603-CAP | Capacitor
C_ERF1 | 4.7uF | CAP0603-CAP | 0603-CAP | Capacitor
C_ERF2 | 0.1uF | CAP0603-CAP | 0603-CAP | Capacitor
C_E_H1 | 4.7uF | CAP0603-CAP | 0603-CAP | Capacitor
C_E_H2 | 0.1uF | CAP0603-CAP | 0603-CAP | Capacitor
C_NR | 0.1uF | CAP0603-CAP | 0603-CAP | Capacitor
C_NRST | 0.1uF | CAP0603-CAP | 0603-CAP | Capacitor
C_NRST1 | 0.1uF | CAP0603-CAP | 0603-CAP | Capacitor
C_NRST2 | 0.1uF | CAP0603-CAP | 0603-CAP | Capacitor
IMU_C1 | 0.1uF | CAP0603-CAP | 0603-CAP | Capacitor
IMU_C2 | 0.1uF | CAP0603-CAP | 0603-CAP | Capacitor
IMU_C3 | 2.2nF | CAP0603-CAP | 0603-CAP | Capacitor
J1 |  | CONN_04 | 1X04 | Multi connection point. Often used as Generic Header-pin footprint for 0.1 inch spaced/style header connections |  |  |  |  |  |  |  |  |  | CONN-09696
J2 | JST_PH | B2B-PH-K-S(LF)(SN) | JST_B2B-PH-K-S(LF)(SN) | PH Series 2 Position 2 mm Pitch Through Hole Top Entry Shrouded Header |  | Connector Header Through Hole 2 position 0.079 _2.00mm_ |  |  |  | JST Sales | B2B-PH-K-S_LF__SN_ | None
J3 | JST_PH | B2B-PH-K-S(LF)(SN) | JST_B2B-PH-K-S(LF)(SN) | PH Series 2 Position 2 mm Pitch Through Hole Top Entry Shrouded Header |  | Connector Header Through Hole 2 position 0.079 _2.00mm_ |  |  |  | JST Sales | B2B-PH-K-S_LF__SN_ | None
J4 |  | CONN_04 | 1X04 | Multi connection point. Often used as Generic Header-pin footprint for 0.1 inch spaced/style header connections |  |  |  |  |  |  |  |  |  | CONN-09696
L1 | 10uH | INDUCTOR1007 | 1007 | Inductors
LEFT_FRONT_EMITTER | EMITTER | EMITTER | EMITTER
NMOS1 | DMN3150LW | DMN3150LW | DMN3150LW
NMOS2 | DMN3150LW | DMN3150LW | DMN3150LW
NMOS3 | DMN3150LW | DMN3150LW | DMN3150LW
NMOS4 | DMN3150LW | DMN3150LW | DMN3150LW
R4 | 4.6k | R-US_M0805 | M0805 | RESISTOR, American symbol |  |  |  |  |  |  |  |  |  |  |  | R
R5 | 4.6k | R-US_M0805 | M0805 | RESISTOR, American symbol |  |  |  |  |  |  |  |  |  |  |  | R
REC_LF | RECEIVER | RECEIVER | RECEIVER
R_B1 | 47k | RESISTOR0603-RES | 0603-RES | Resistor
R_B2 | 47k | RESISTOR0603-RES | 0603-RES | Resistor
R_ED1 | 5.6 | RESISTOR0603-RES | 0603-RES | Resistor
R_ED2 | 5.6 | RESISTOR0603-RES | 0603-RES | Resistor
R_ED_PD | 47k | RESISTOR0603-RES | 0603-RES | Resistor
R_EH1 | 5.6 | RESISTOR0603-RES | 0603-RES | Resistor
R_EH2 | 5.6 | RESISTOR0603-RES | 0603-RES | Resistor
R_EH_PD | 47k | RESISTOR0603-RES | 0603-RES | Resistor
R_ELF | 10 | RESISTOR0603-RES | 0603-RES | Resistor
R_ELF_PD | 47k | RESISTOR0603-RES | 0603-RES | Resistor
R_ERF | 30 | RESISTOR0603-RES | 0603-RES | Resistor
R_ERF_PD | 47k | RESISTOR0603-RES | 0603-RES | Resistor
R_PWR1 | 100 Ohm | RESISTOR0603-RES | 0603-RES | Resistor
R_PWR3 | 100 Ohm | RESISTOR0603-RES | 0603-RES | Resistor
R_PWR4 | 100 Ohm | RESISTOR0603-RES | 0603-RES | Resistor
R_RLD | 1.8k | RESISTOR0603-RES | 0603-RES | Resistor
R_RLF | 1.8k | RESISTOR0603-RES | 0603-RES | Resistor
R_RLH | 1.8k | RESISTOR0603-RES | 0603-RES | Resistor
R_RRD | 1.8k | RESISTOR0603-RES | 0603-RES | Resistor
R_RRF | 1.8k | RESISTOR0603-RES | 0603-RES | Resistor
R_RRH | 1.8k | RESISTOR0603-RES | 0603-RES | Resistor
R_VM1 | 70k | RESISTOR0603-RES | 0603-RES | Resistor
R_VM2 | 40k | RESISTOR0603-RES | 0603-RES | Resistor
R_VM3 | 500m | RESISTOR0603-RES | 0603-RES | Resistor
R_VM4 | 500m | RESISTOR0603-RES | 0603-RES | Resistor
R_VM5 | 10k | RESISTOR0603-RES | 0603-RES | Resistor
S2 |  | SWITCH-SPSTPTH | SWITCH-SPDT | SPST Switch
T1 |  | TESTPOINTROUND2MM | TESTPOINT_ROUND_2MM | Test Point
T2 |  | TESTPOINTROUND2MM | TESTPOINT_ROUND_2MM | Test Point
T3 |  | TESTPOINTROUND2MM | TESTPOINT_ROUND_2MM | Test Point
T4 |  | TESTPOINTROUND2MM | TESTPOINT_ROUND_2MM | Test Point
T5 |  | TESTPOINTROUND2MM | TESTPOINT_ROUND_2MM | Test Point
T6 |  | TESTPOINTROUND2MM | TESTPOINT_ROUND_2MM | Test Point
TP7 |  | TESTPOINTROUND2MM | TESTPOINT_ROUND_2MM | Test Point
TP8 |  | TESTPOINTROUND2MM | TESTPOINT_ROUND_2MM | Test Point
TP9 |  | TESTPOINTROUND2MM | TESTPOINT_ROUND_2MM | Test Point
TP10 |  | TESTPOINTROUND2MM | TESTPOINT_ROUND_2MM | Test Point
TP11 |  | TESTPOINTROUND2MM | TESTPOINT_ROUND_2MM | Test Point
TP12 |  | TESTPOINTROUND2MM | TESTPOINT_ROUND_2MM | Test Point
TP13 |  | TESTPOINTROUND2MM | TESTPOINT_ROUND_2MM | Test Point
U$3 | TPS73633(SOT-23) | TPS73633(SOT-23) | TPS73633(SOT-23)
U$4 | TPS76850(SOIC-8) | TPS76850(SOIC-8) | TPS76850(SOIC-8)
U$5 | 6P_HEADER | 6P_HEADER | 6P_HEADER | Generic 6P header
U$6 | 6P_HEADER | 6P_HEADER | 6P_HEADER | Generic 6P header
U$7 | RECEIVER | RECEIVER | RECEIVER
U$8 | RECEIVER | RECEIVER | RECEIVER
U$9 | RECEIVER | RECEIVER | RECEIVER
U$11 | EMITTER | EMITTER | EMITTER
U$13 | EMITTER | EMITTER | EMITTER
U$14 | SPARKFUN-SPDT | SPARKFUN-SPDT | SPDT
U$15 | SPARKFUN-SPDT | SPARKFUN-SPDT | SPDT
U$16 | SPLITTER | SPLITTER | SPLITTER
U$17 | EMITTER | EMITTER | EMITTER
U$18 | EMITTER | EMITTER | EMITTER
U$19 | EMITTER | EMITTER | EMITTER
U$20 | RECEIVER | RECEIVER | RECEIVER
U$21 | RECEIVER | RECEIVER | RECEIVER
U$22 | SPLITTER | SPLITTER | SPLITTER
U$23 | BD60HC5WEFJ | BD60HC5WEFJ | SOIC127P600X100-9N
U2 | DRV8848PWPR | DRV8848PWPR | SOP65P640X120-17N | None | Unavailable | 2A Dual H-Bridge Motor Driver _PWM Control_ 16-HTSSOP -40 to 85 |  |  |  | Texas Instruments | DRV8848PWPR | HTSSOP-16 Texas Instruments | None
U6 | MPU-6000 | MPU-6000 | QFN-24-EP | Invensense MPU-6000 6-Axis Gryoscope/Accelerometer |  |  |  |  |  |  |  |  |  | IC-11089 | SEN-11234
X1 | RASPI_GPIO_B+#_PIN | RASPI_GPIO_B+#_PIN | RASPI_GPIO_B+_PIN | 2x20 header connector, all pins connected

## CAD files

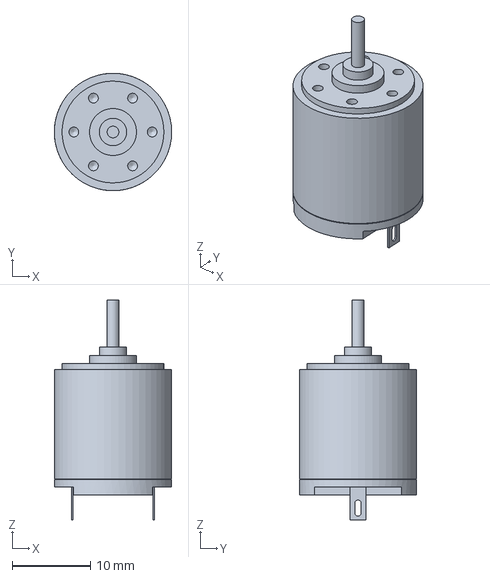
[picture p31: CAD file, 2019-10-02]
3D-Models/1516_SR_3D-CAD/1516T_SR/1516T_SR.stp
15.0 x 15.0 x 28.1 mm

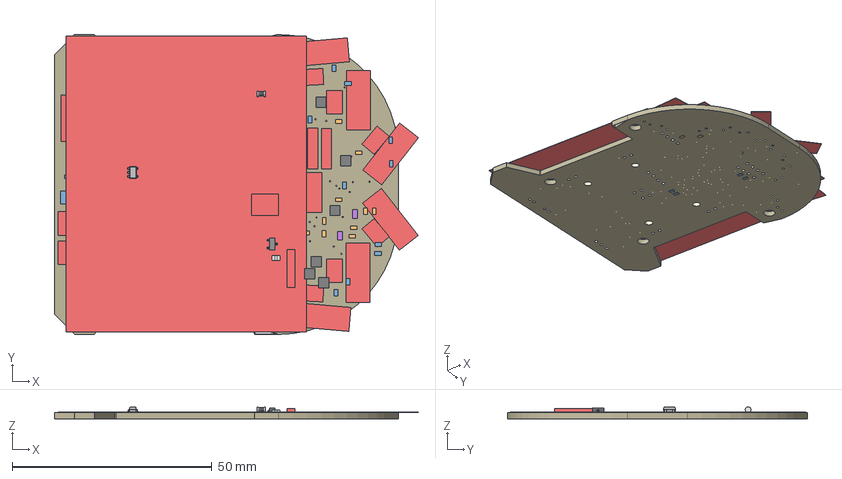
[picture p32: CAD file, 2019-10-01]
3D-Models/1717_SR_3D-CAD/1717T_SR/routed-micromouse-board 1.1.2 v1_CAD.step
91.0 x 75.0 x 3.13 mm
Board
1.4 uF x 27
1.8k x 16
EMITTER x 6
MY_MM_MOTOR_MOUNT
RECEIVER x 6
DMN3150LW x 4
STM32F103RET6
SN74HC151DR
DRV8848PWPR
ACS712ELCTR-20A-T
1k
1X04 x 2
RESET
1k_1 x 7
JST_CONNECTOR_FEMALE x 2
SWITCH-SPDT
500m x 3
LM321MFX
MOLEX-1X2 x 2
TPS76850(SOIC-8)
0.1uF x 7
TPS73633(SOT-23)
47uF x 2
green
10uH
0.1uF_1
MPU-6000
TESTPOINT_ROUND_2MM x 6
SOT23
1k_2
1X04 (1)

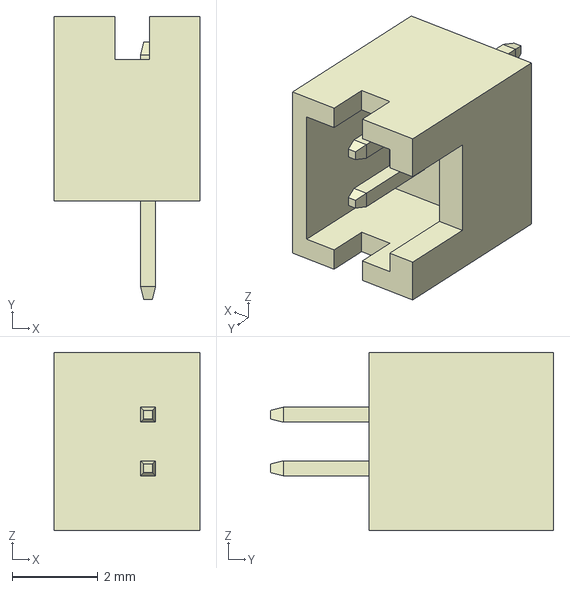
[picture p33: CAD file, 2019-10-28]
3D-Models/Micromouse-EDU-3D/DF13_CL0536-0101-9-00_3dstep/DF13-2P-1.25DSA.stp
3.40 x 6.60 x 4.15 mm

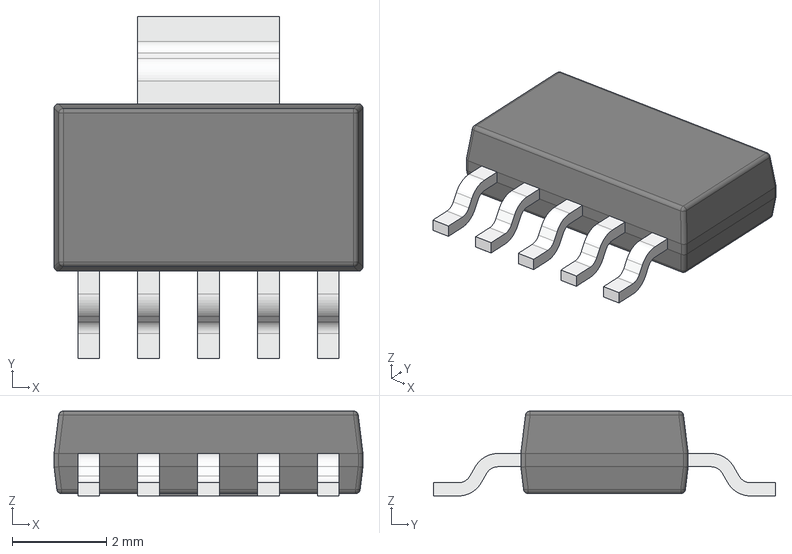
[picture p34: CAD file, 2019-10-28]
3D-Models/Micromouse-EDU-3D/discrete-smd-1.snapshot.88/custom/TI_DCQ_R-PDSO-G6.stp
6.55 x 7.26 x 1.80 mm

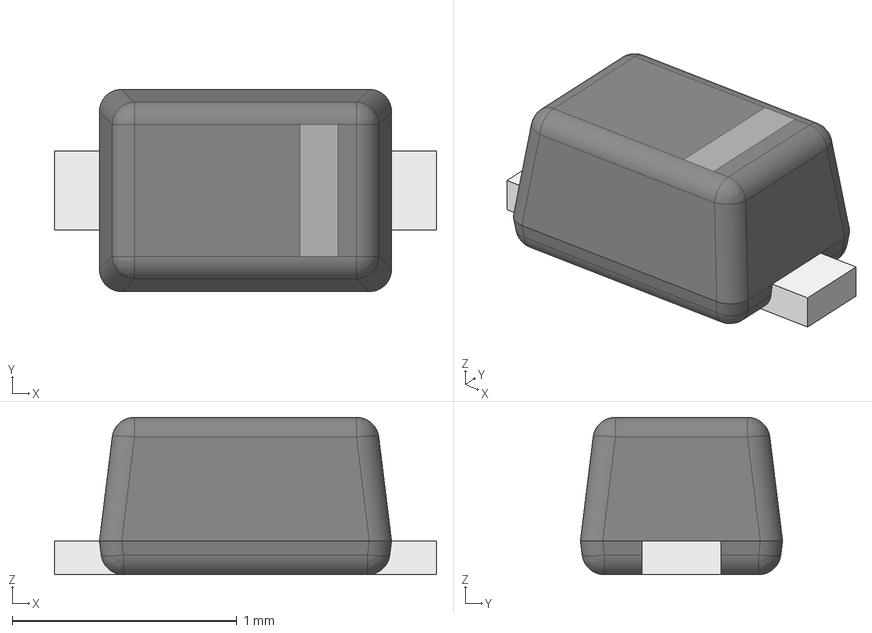
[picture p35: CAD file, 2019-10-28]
3D-Models/Micromouse-EDU-3D/discrete-smd-1.snapshot.88/SC-79.stp
1.70 x 0.9 x 0.7 mm

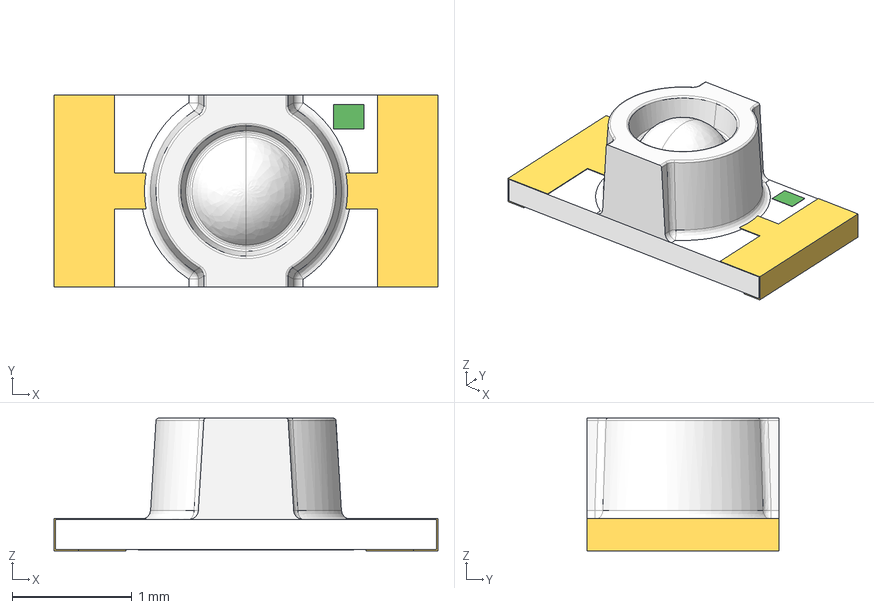
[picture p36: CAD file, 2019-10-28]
3D-Models/Micromouse-EDU-3D/led-smd-1206-1.snapshot.2/SML-LXLC1206.stp
3.21 x 1.60 x 1.11 mm

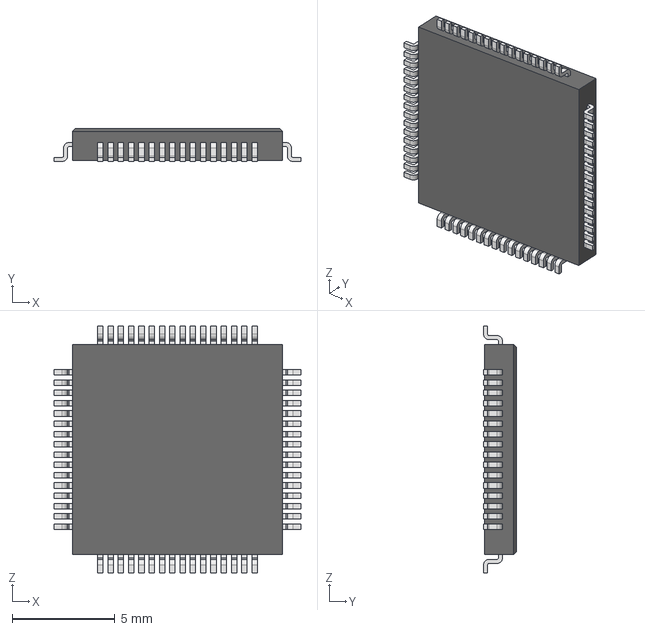
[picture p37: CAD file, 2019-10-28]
3D-Models/Micromouse-EDU-3D/lqfp-64-pin-1.snapshot.3/STM32F103RET6.step
12.0 x 1.60 x 12.0 mm

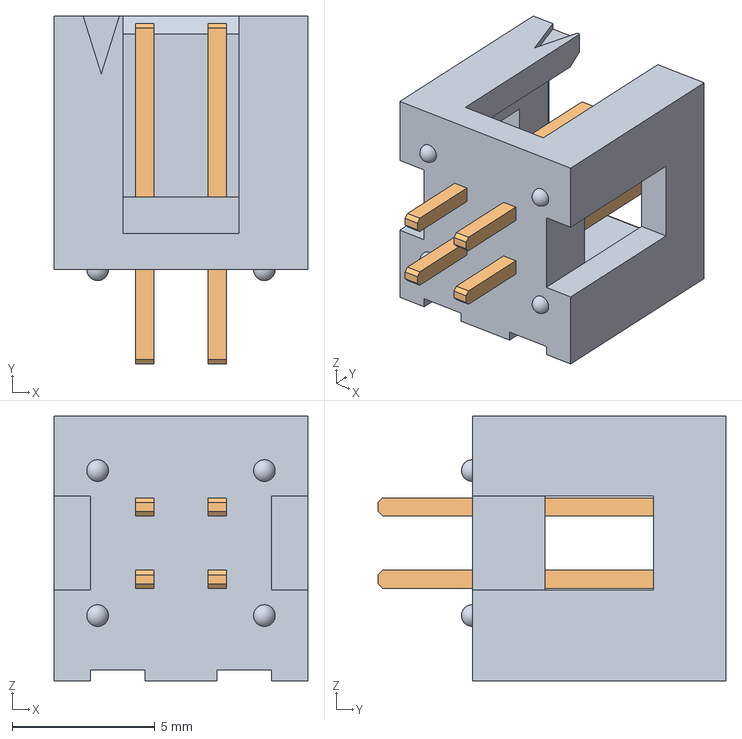
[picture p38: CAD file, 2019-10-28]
3D-Models/Micromouse-EDU-3D/PARTserver0201910280535028630881410e898ce/HTSS-102-01-G-D.stp
8.89 x 12.2 x 9.27 mm
_HTSS-102-01-D_header
_T-1S6-02-01-D_HTSS

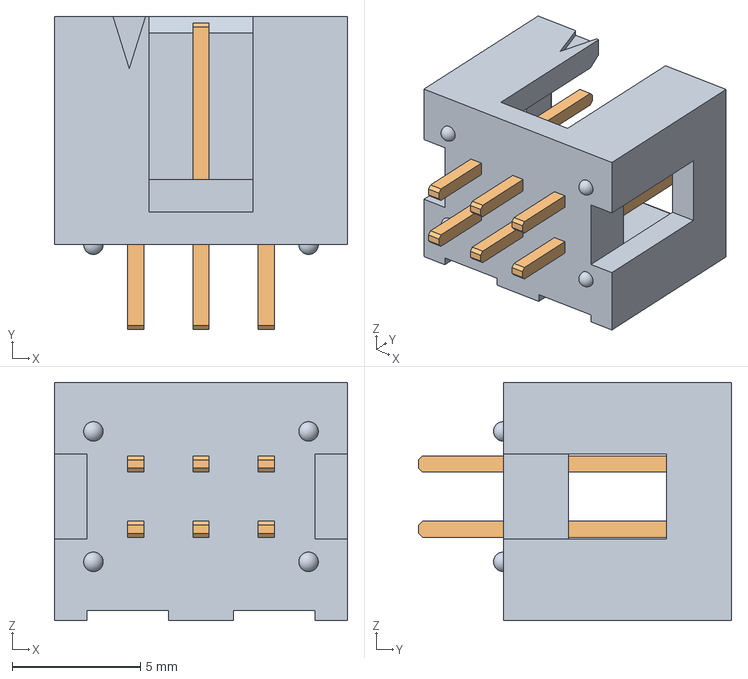
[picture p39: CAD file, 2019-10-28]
3D-Models/Micromouse-EDU-3D/PARTserver0201910280537269420897010e898ce/HTSS-103-01-G-D.stp
11.4 x 12.2 x 9.27 mm
_HTSS-103-01-D_header
_T-1S6-03-01-D_HTSS

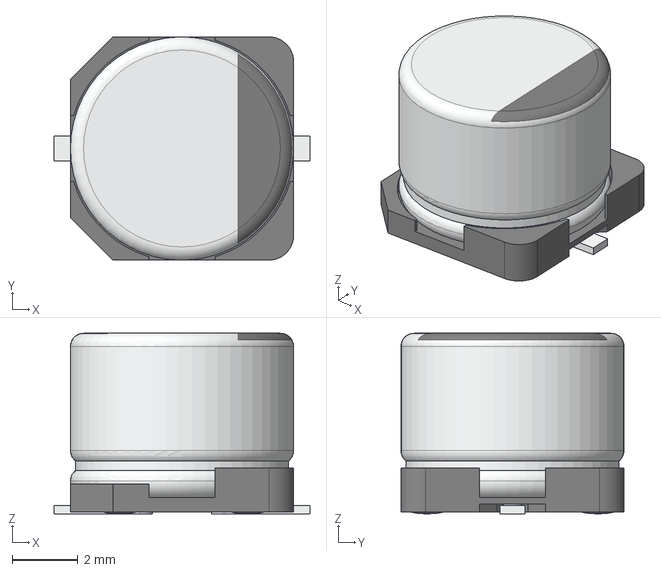
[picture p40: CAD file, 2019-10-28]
3D-Models/Micromouse-EDU-3D/passive-smd-1.snapshot.154/Capacitors/CAPAE-D6.3x5.4.stp
7.80 x 6.80 x 5.50 mm

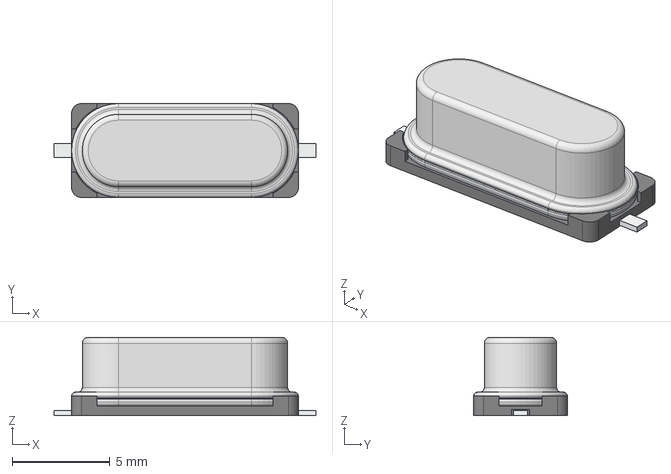
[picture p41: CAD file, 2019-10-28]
3D-Models/Micromouse-EDU-3D/passive-smd-1.snapshot.154/Crystals/HC-49SM.stp
13.4 x 4.80 x 4.00 mm

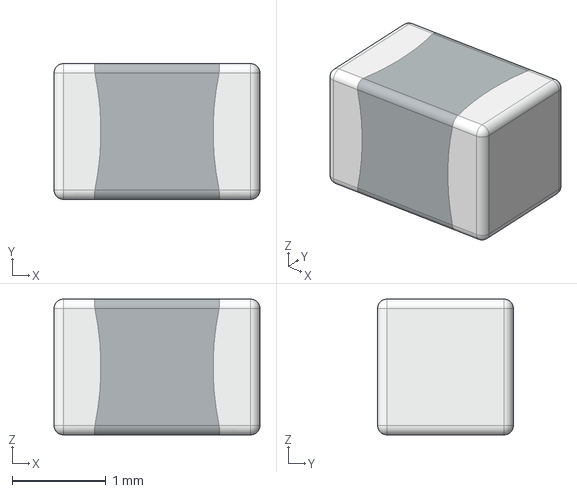
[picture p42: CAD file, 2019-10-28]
3D-Models/Micromouse-EDU-3D/passive-smd-1.snapshot.154/Inductors/INDC-0805-T1.45.stp
2.20 x 1.45 x 1.45 mm

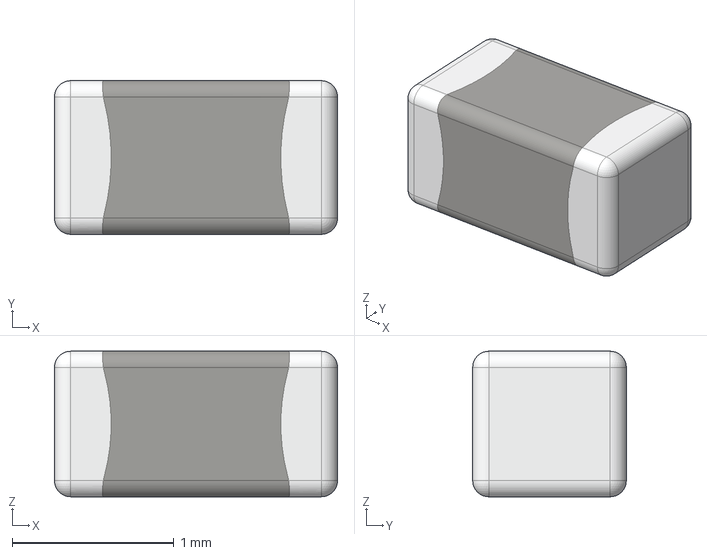
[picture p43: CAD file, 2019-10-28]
3D-Models/Micromouse-EDU-3D/passive-smd-1.snapshot.154/Resistors/NTC-0603-T0.9.stp
1.75 x 0.95 x 0.9 mm

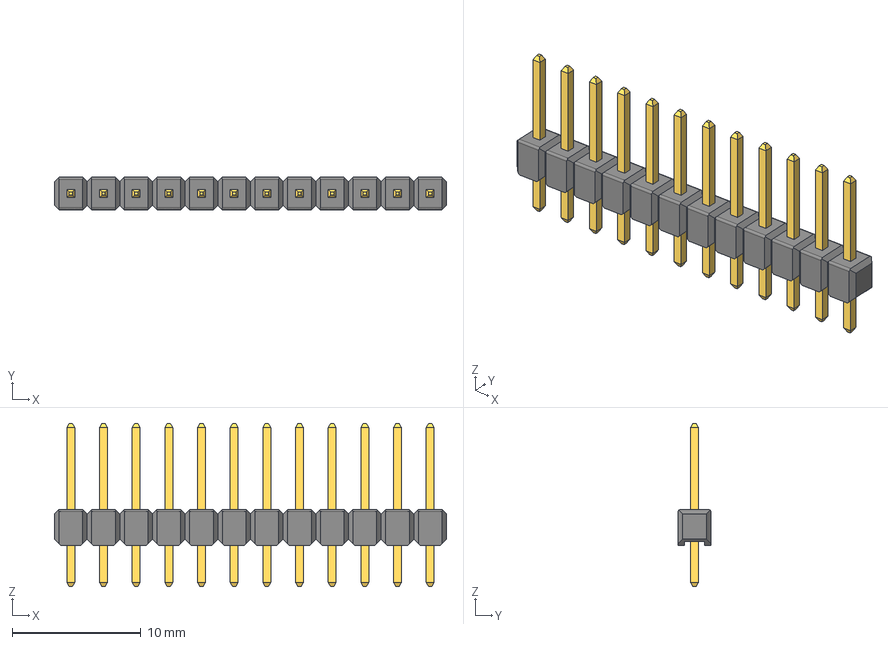
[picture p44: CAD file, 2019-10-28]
3D-Models/Micromouse-EDU-3D/pin-headers-1.snapshot.5/Pin Header 1x12 TH Pitch 2.54mm.stp
30.5 x 2.54 x 12.7 mm

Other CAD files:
3D-Models/Micromouse-EDU-3D/qfn24-4x4-1.snapshot.1/QFN24(4X4).STEP
3D-Models/Micromouse-EDU-3D/raspi/SSW-120-01-G-D.stp
3D-Models/Micromouse-EDU-3D/reciever.step
3D-Models/Micromouse-EDU-3D/small-slide-switch-1.snapshot.1/switch small.stp
3D-Models/1516_SR_3D-CAD/1516T_SR/1516T_SR.igs
3D-Models/1516_SR_3D-CAD/1516T_SR/1516T_SR.x_t
3D-Models/1717_SR_3D-CAD/1717T_SR/1717T_SR.igs
3D-Models/1717_SR_3D-CAD/1717T_SR/1717T_SR.stp
3D-Models/1717_SR_3D-CAD/1717T_SR/1717T_SR.x_t
3D-Models/Micromouse-EDU-3D/B2B-PH-K-S(LF)(SN)--3DModel-STEP-56544.STEP
3D-Models/Micromouse-EDU-3D/EVPAA-002K_202K_402W_602W_802Q.STEP
3D-Models/Micromouse-EDU-3D/KMR431GULCLFS-pcb-part-libraries/gears-wheel-old v1.step
3D-Models/Micromouse-EDU-3D/MLCC.SLDPRT
3D-Models/Micromouse-EDU-3D/PushBtn v1.step
3D-Models/Micromouse-EDU-3D/PushBtn.SLDPRT
3D-Models/Micromouse-EDU-3D/SFH 3310--3DModel-STEP-56544.STEP
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

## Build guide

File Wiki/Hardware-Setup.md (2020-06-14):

# Hardware Setup :zap:

### Useful Links
- [Microcontroller (STM32F103RET6) Datasheet](https://static6.arrow.com/aropdfconversion/e79ced670cb149ee24e5f1de20d472baa245090d/403en.stm32f103rc.pdf)
- [Motor Encoder (EI2-128) Datasheet](https://www.faulhaber.com/fileadmin/Import/Media/EN_IE2-1024_DFF.pdf)
- [Motor Driver Datasheet](http://www.ti.com/lit/ds/symlink/drv8848.pdf)
- [Motor Datasheet (1717T006)](https://www.micromo.com/media/pdfs/1717_SR.pdf)
- [Motor Encoder Interface](https://www.sparkfun.com/products/10651)
- [Blue Pill pinout](https://github.com/uga-robotics/MicromouseV1/blob/master/docs/datasheets/STM32bluepillarduinoguide.pdf)

### Next
<!-- Link to software repo README -->
Go to [software setup](https://github.com/Spain2394/MicromouseV1/blob/master/Wiki/Software-Setup.md)

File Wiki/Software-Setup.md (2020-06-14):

# Software Setup :alien:
This page contains the dependencies and needed drivers to operate the micromouse.

--------
# Getting started visit [MicromouseV1_Software](https://github.com/uga-robotics/MicromouseV1_Software)

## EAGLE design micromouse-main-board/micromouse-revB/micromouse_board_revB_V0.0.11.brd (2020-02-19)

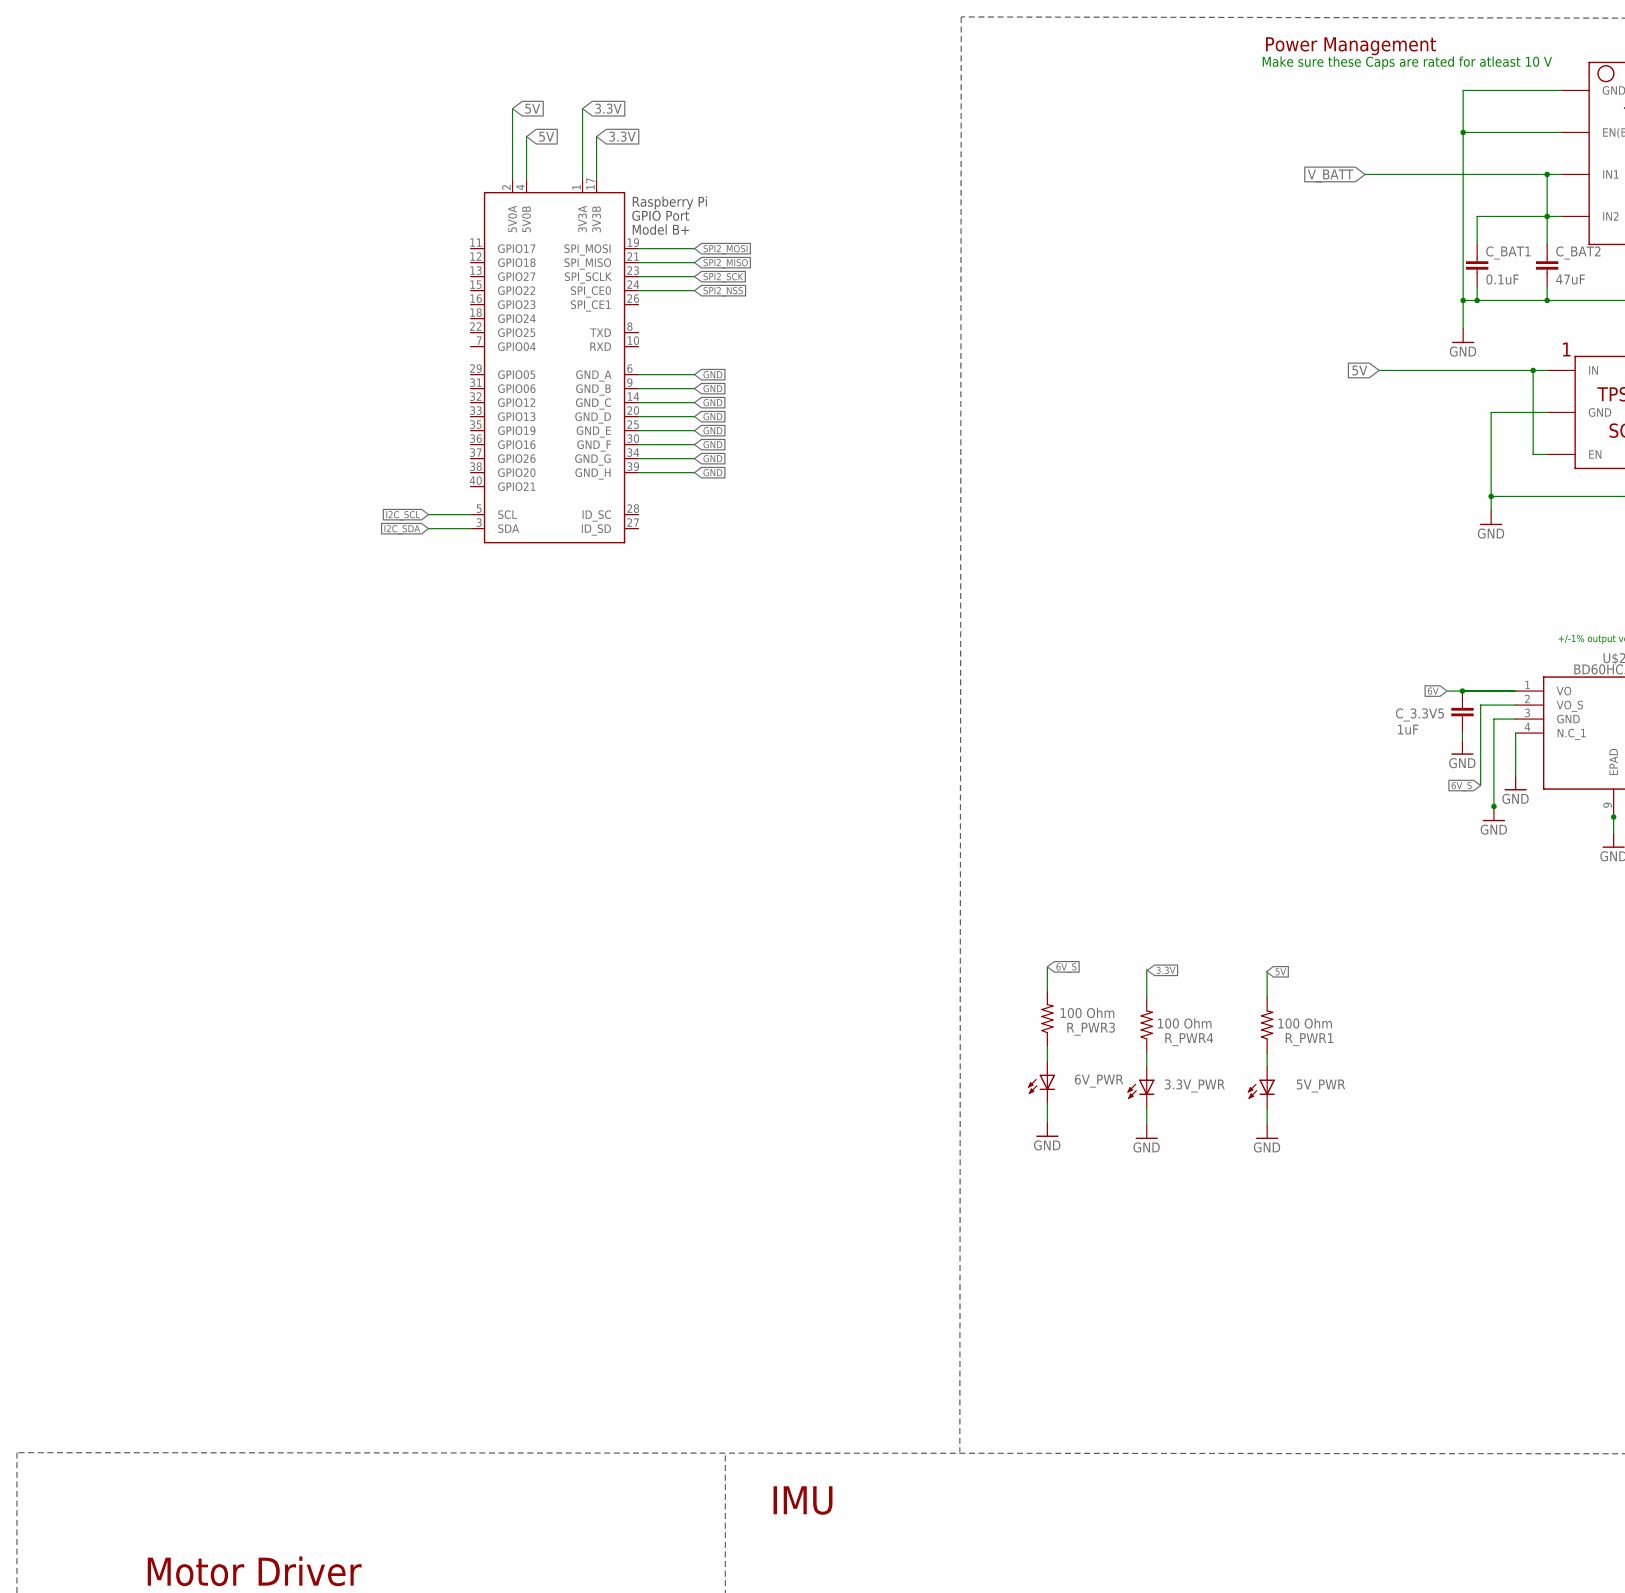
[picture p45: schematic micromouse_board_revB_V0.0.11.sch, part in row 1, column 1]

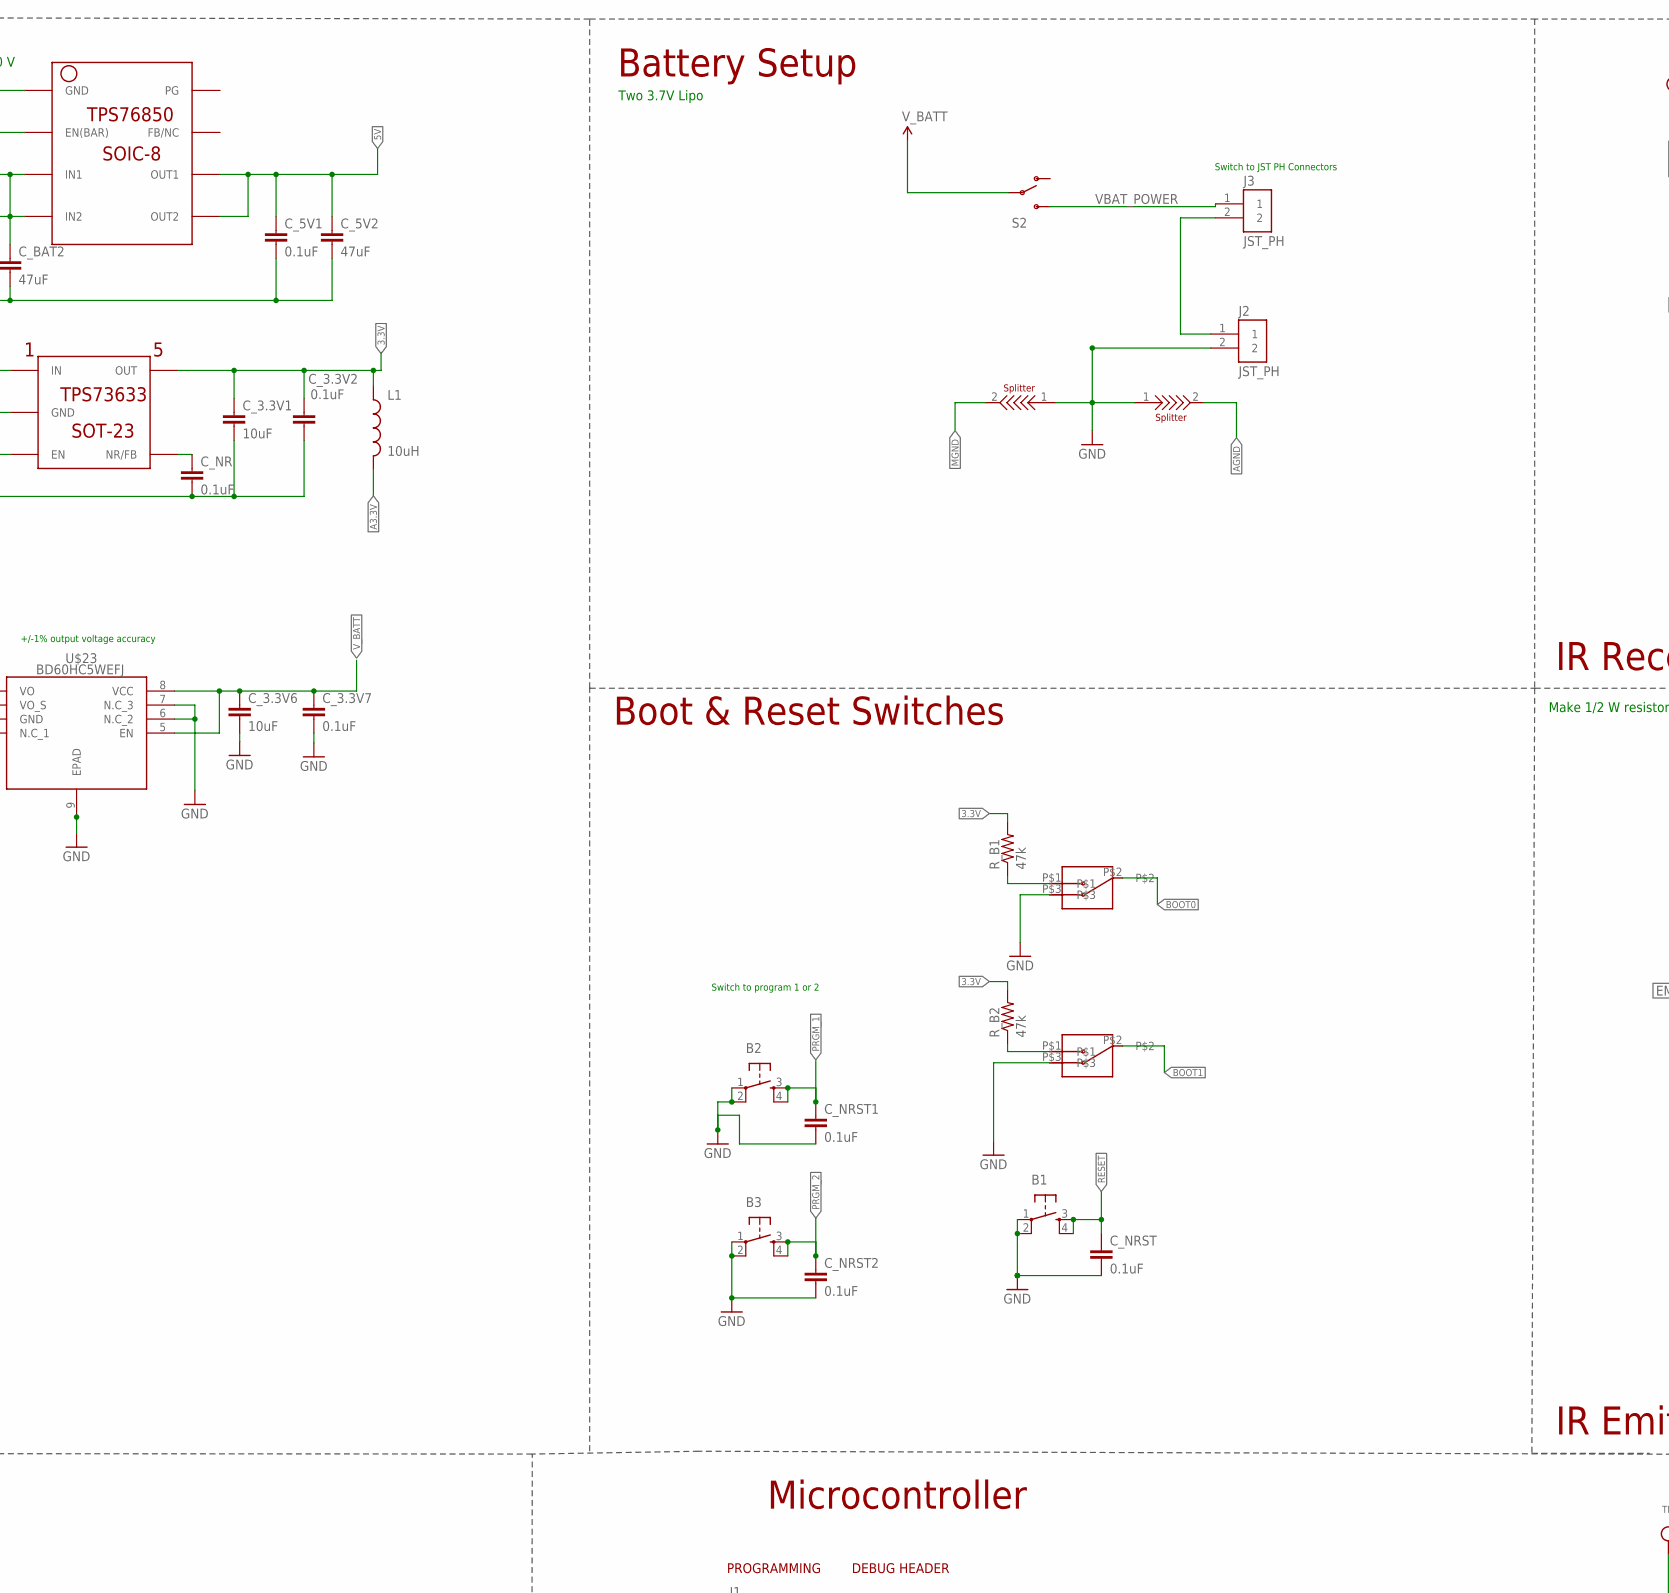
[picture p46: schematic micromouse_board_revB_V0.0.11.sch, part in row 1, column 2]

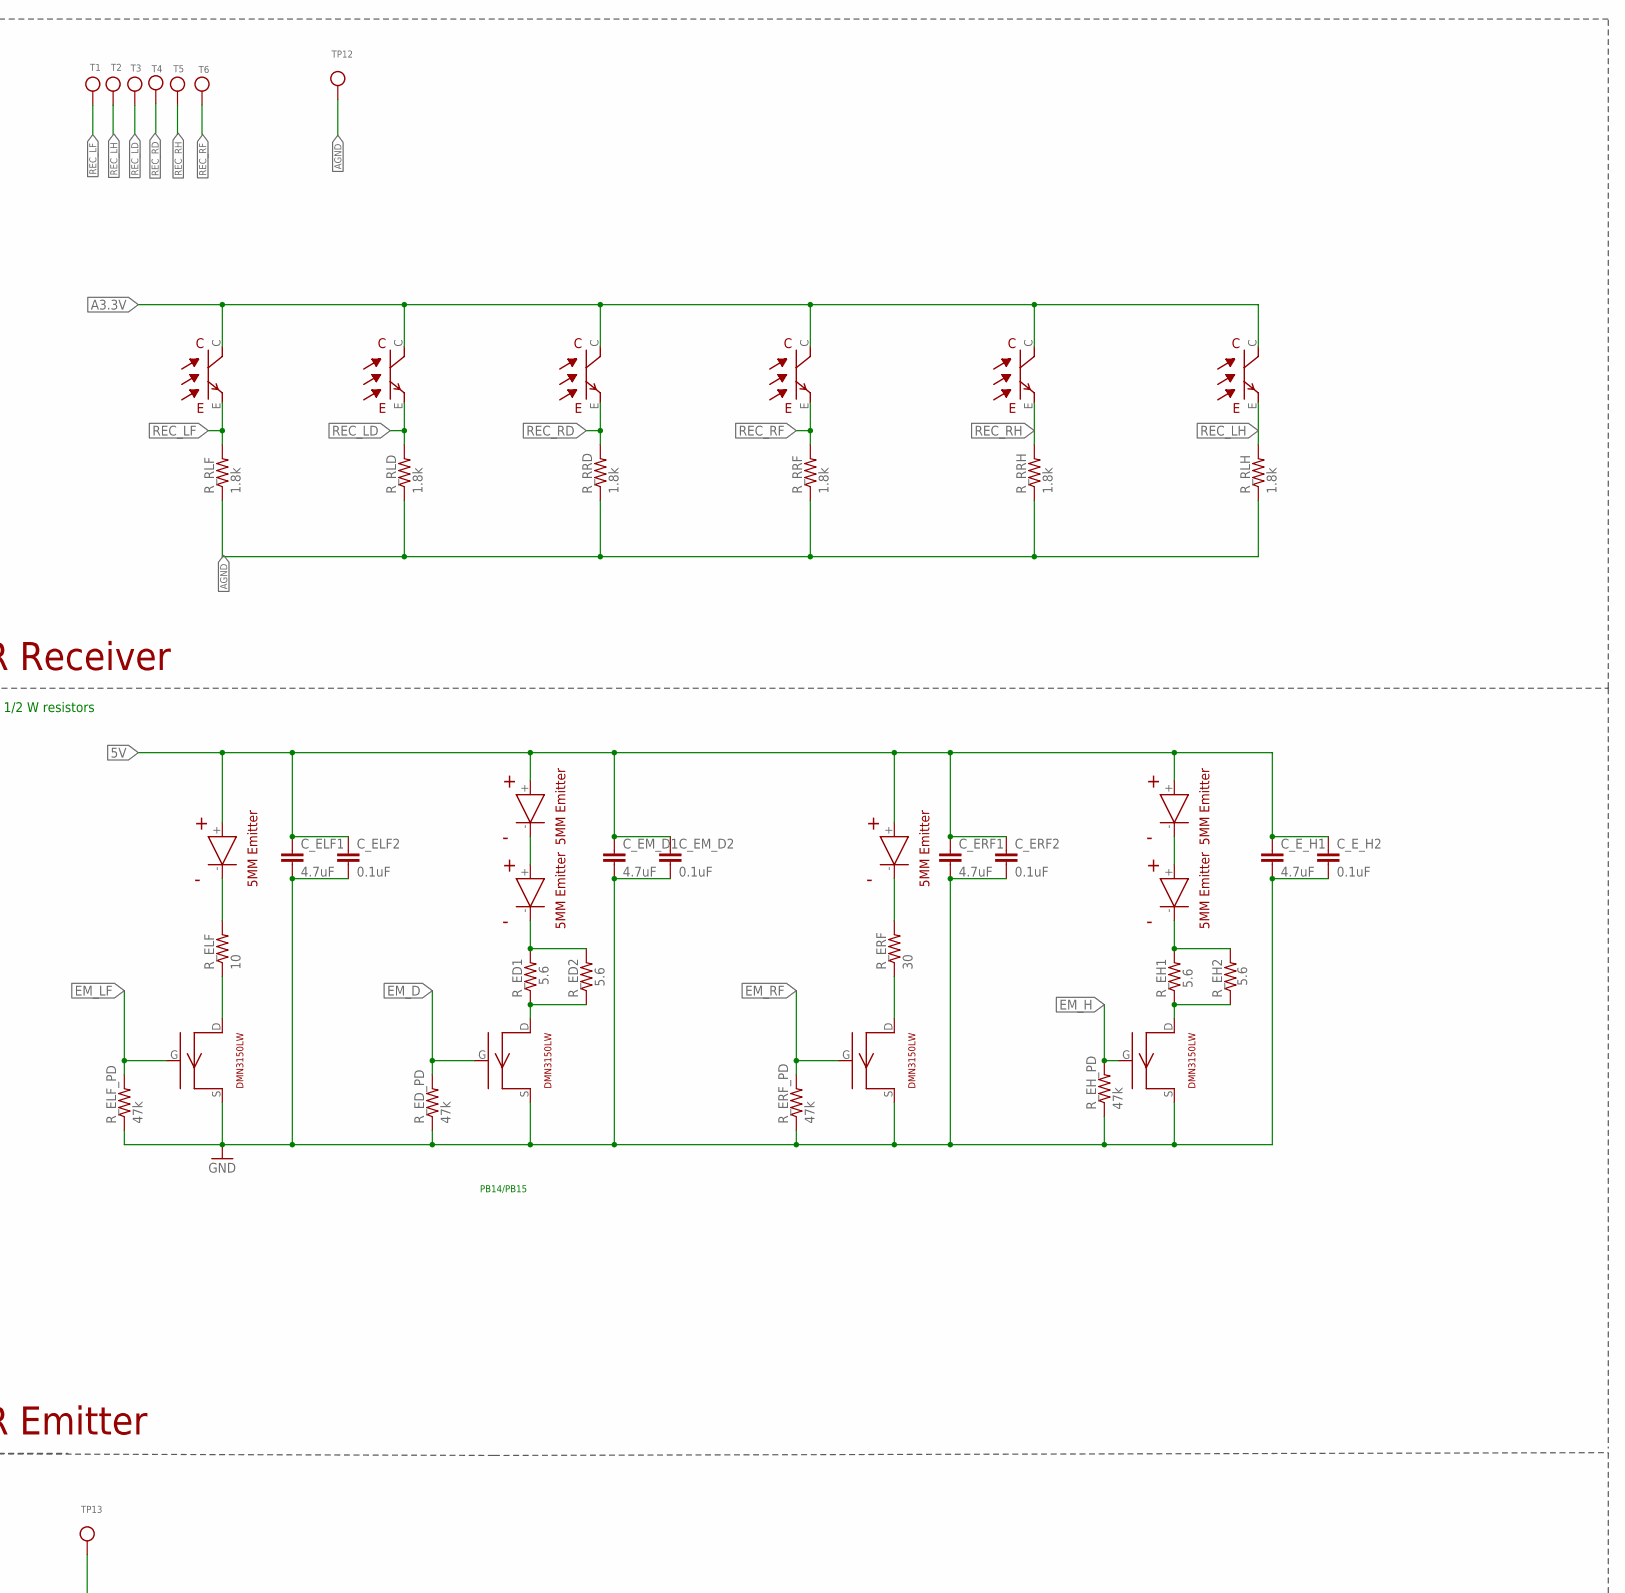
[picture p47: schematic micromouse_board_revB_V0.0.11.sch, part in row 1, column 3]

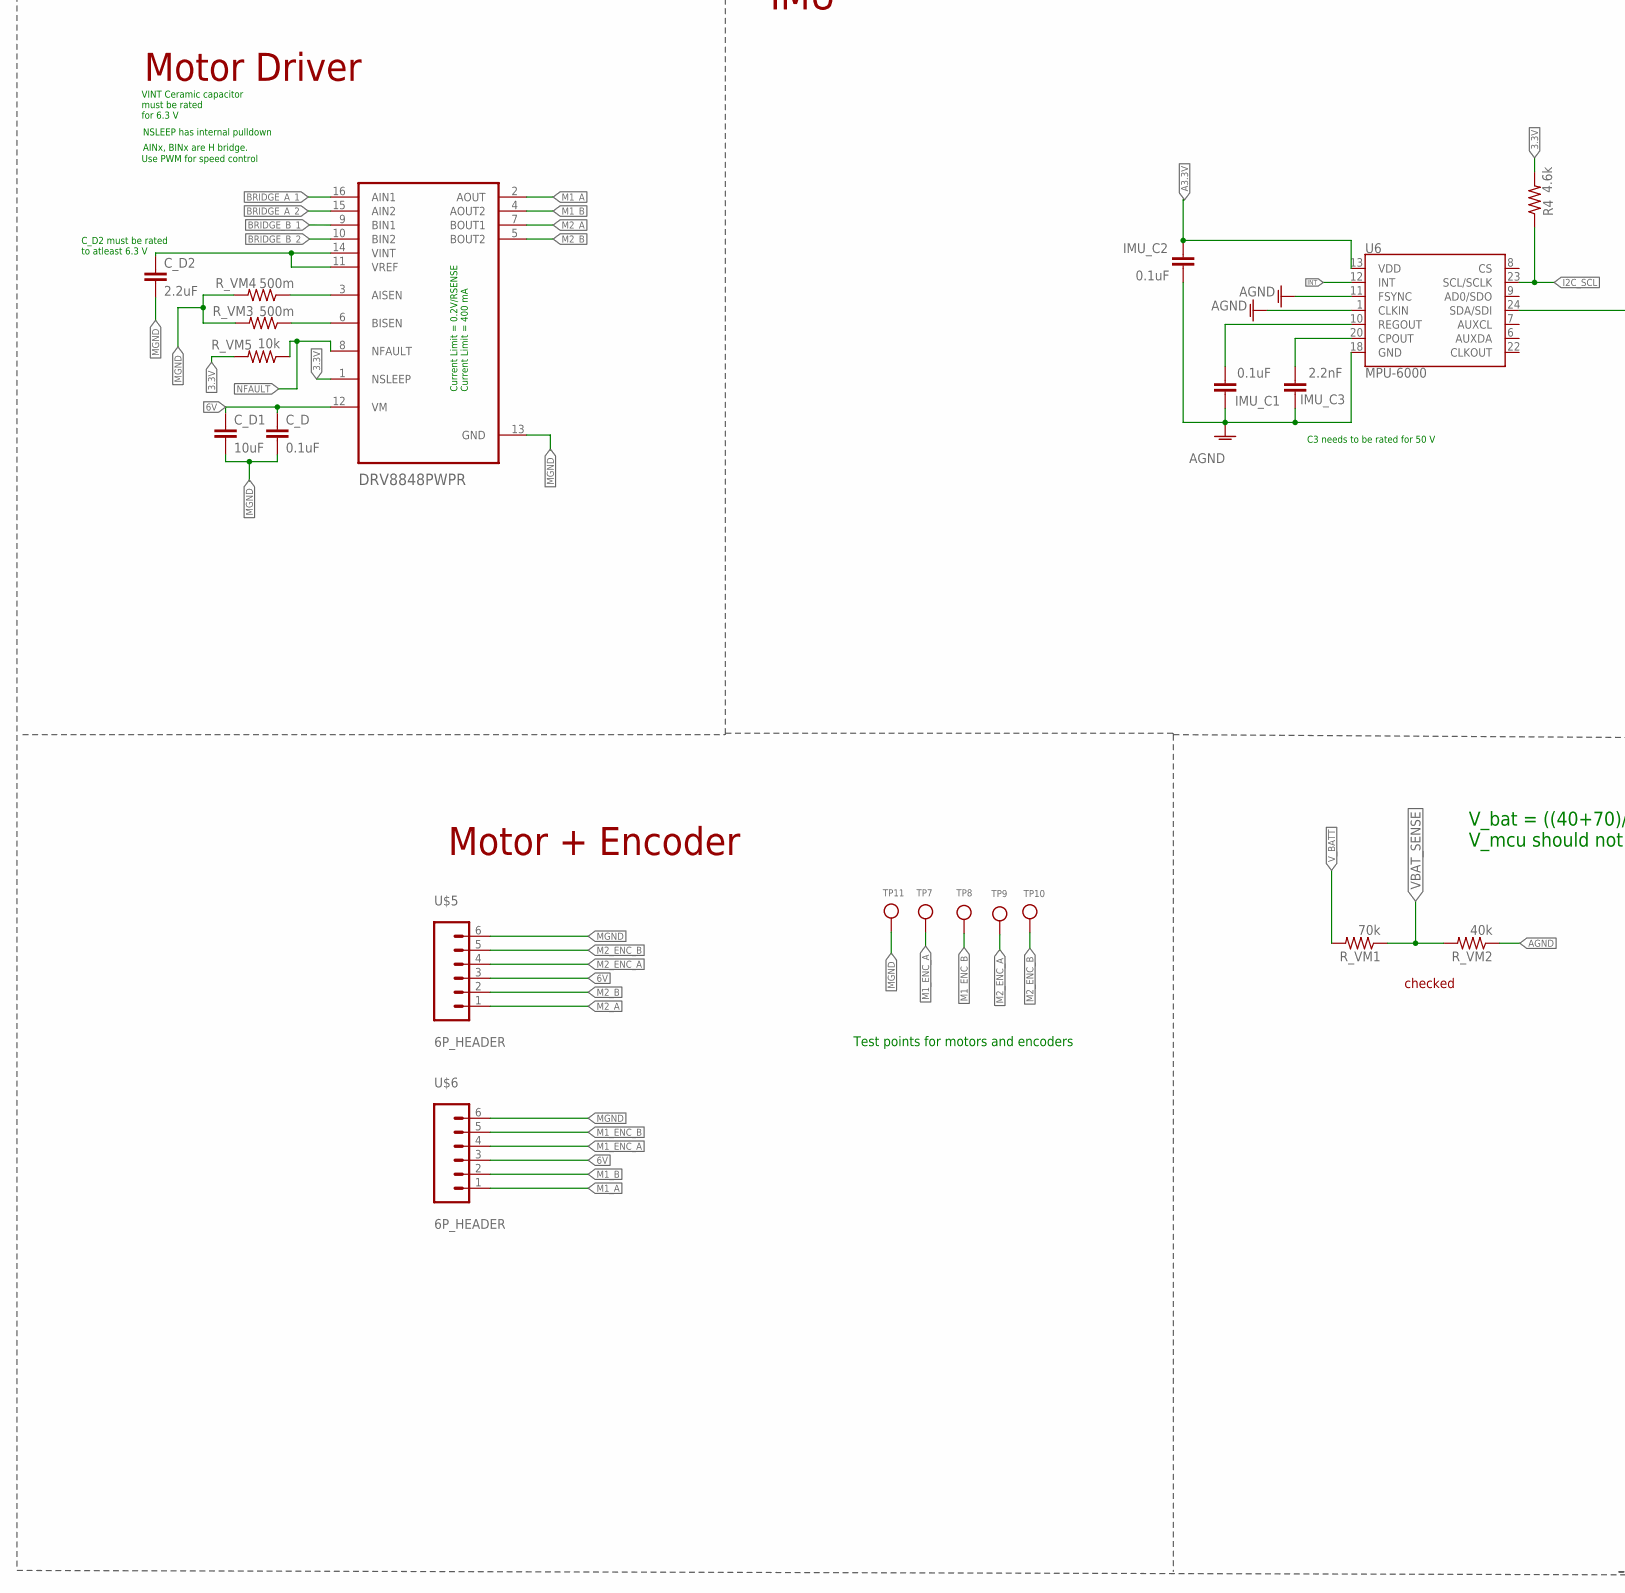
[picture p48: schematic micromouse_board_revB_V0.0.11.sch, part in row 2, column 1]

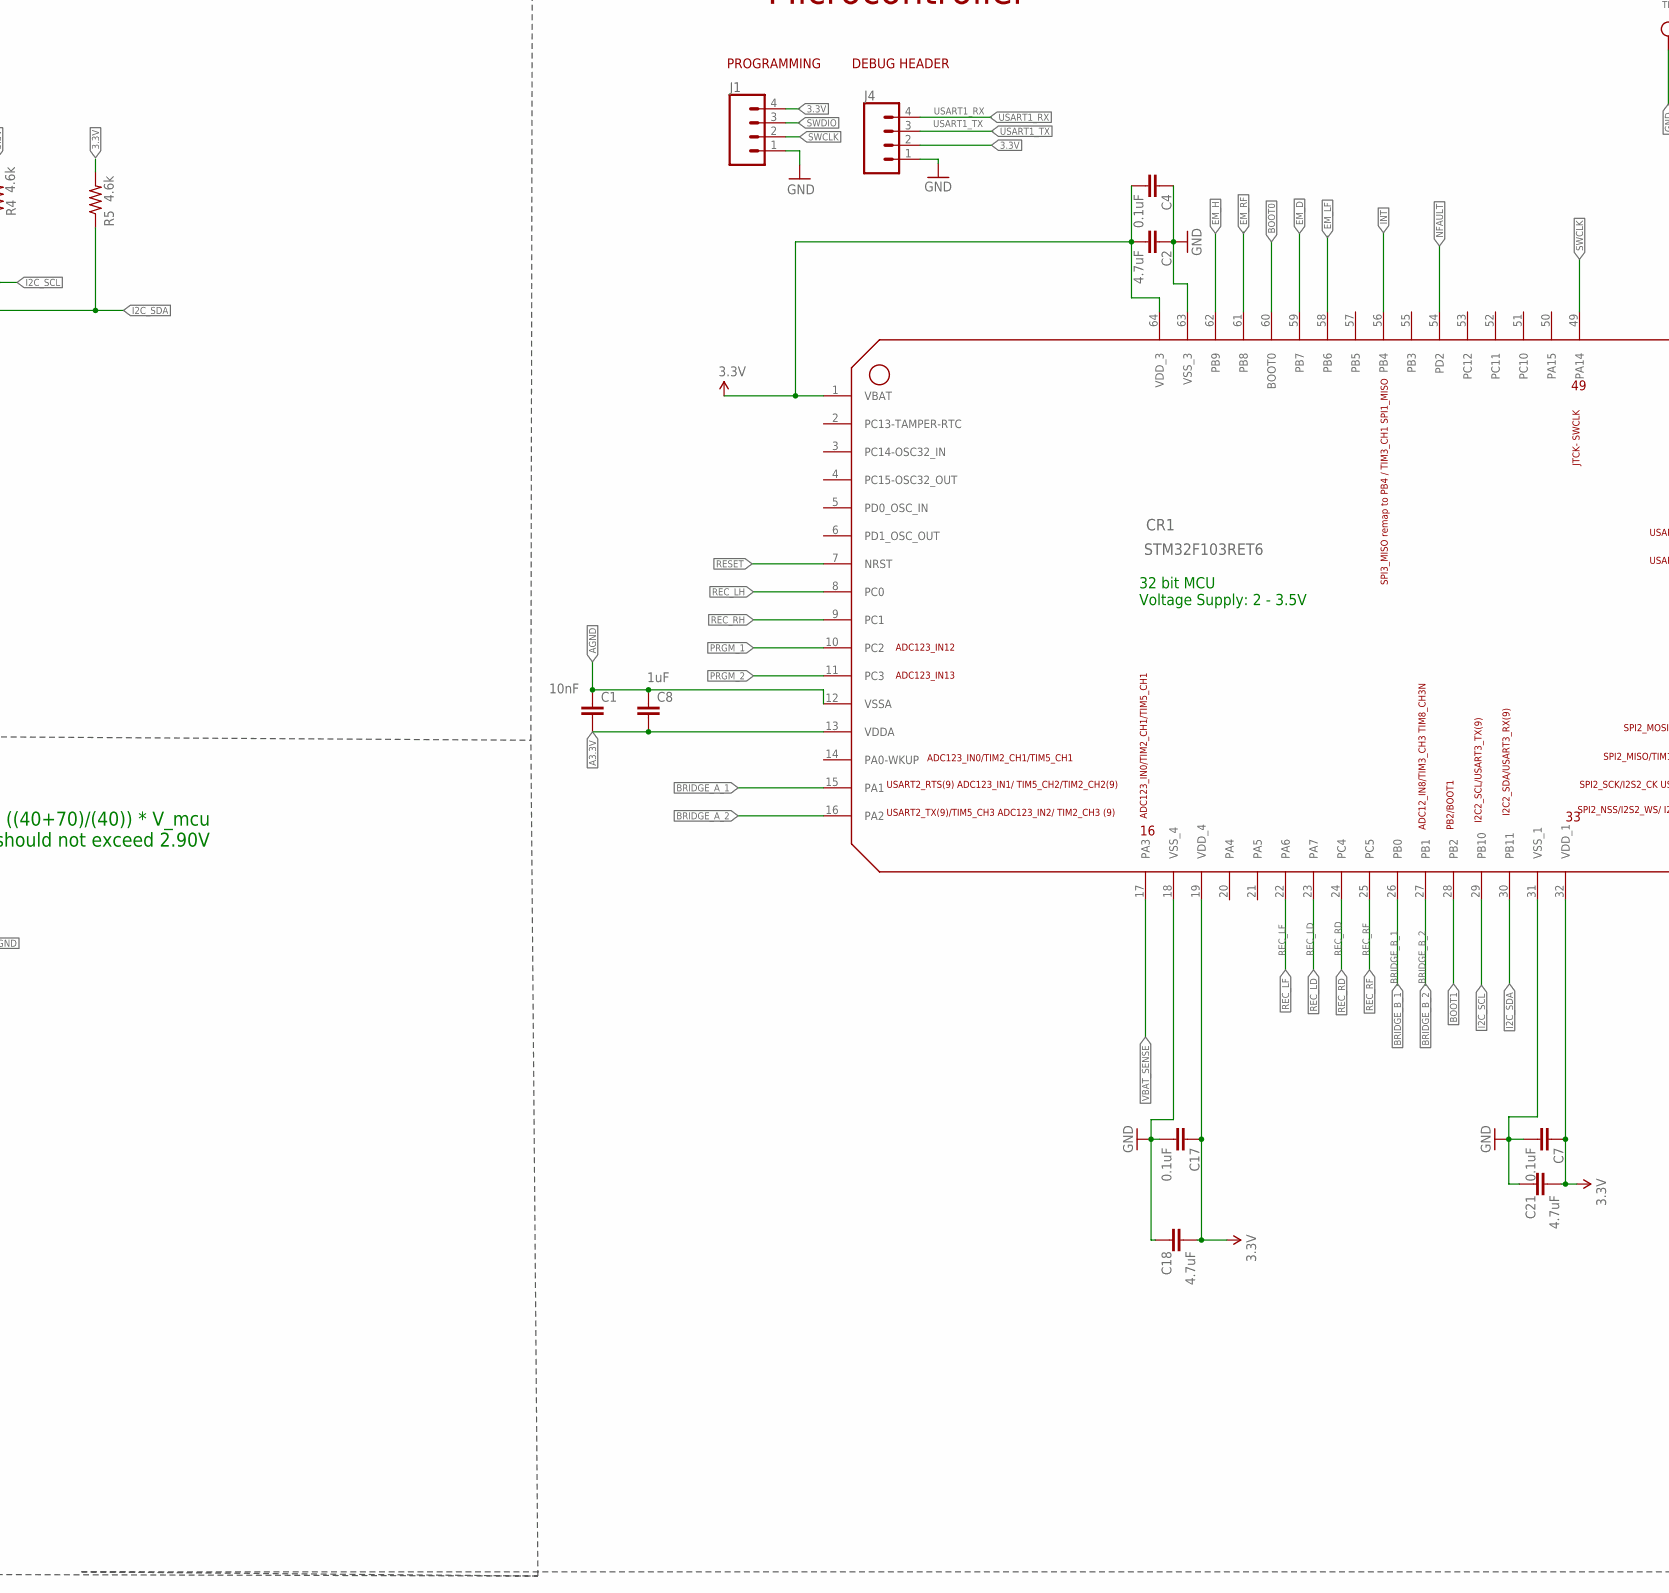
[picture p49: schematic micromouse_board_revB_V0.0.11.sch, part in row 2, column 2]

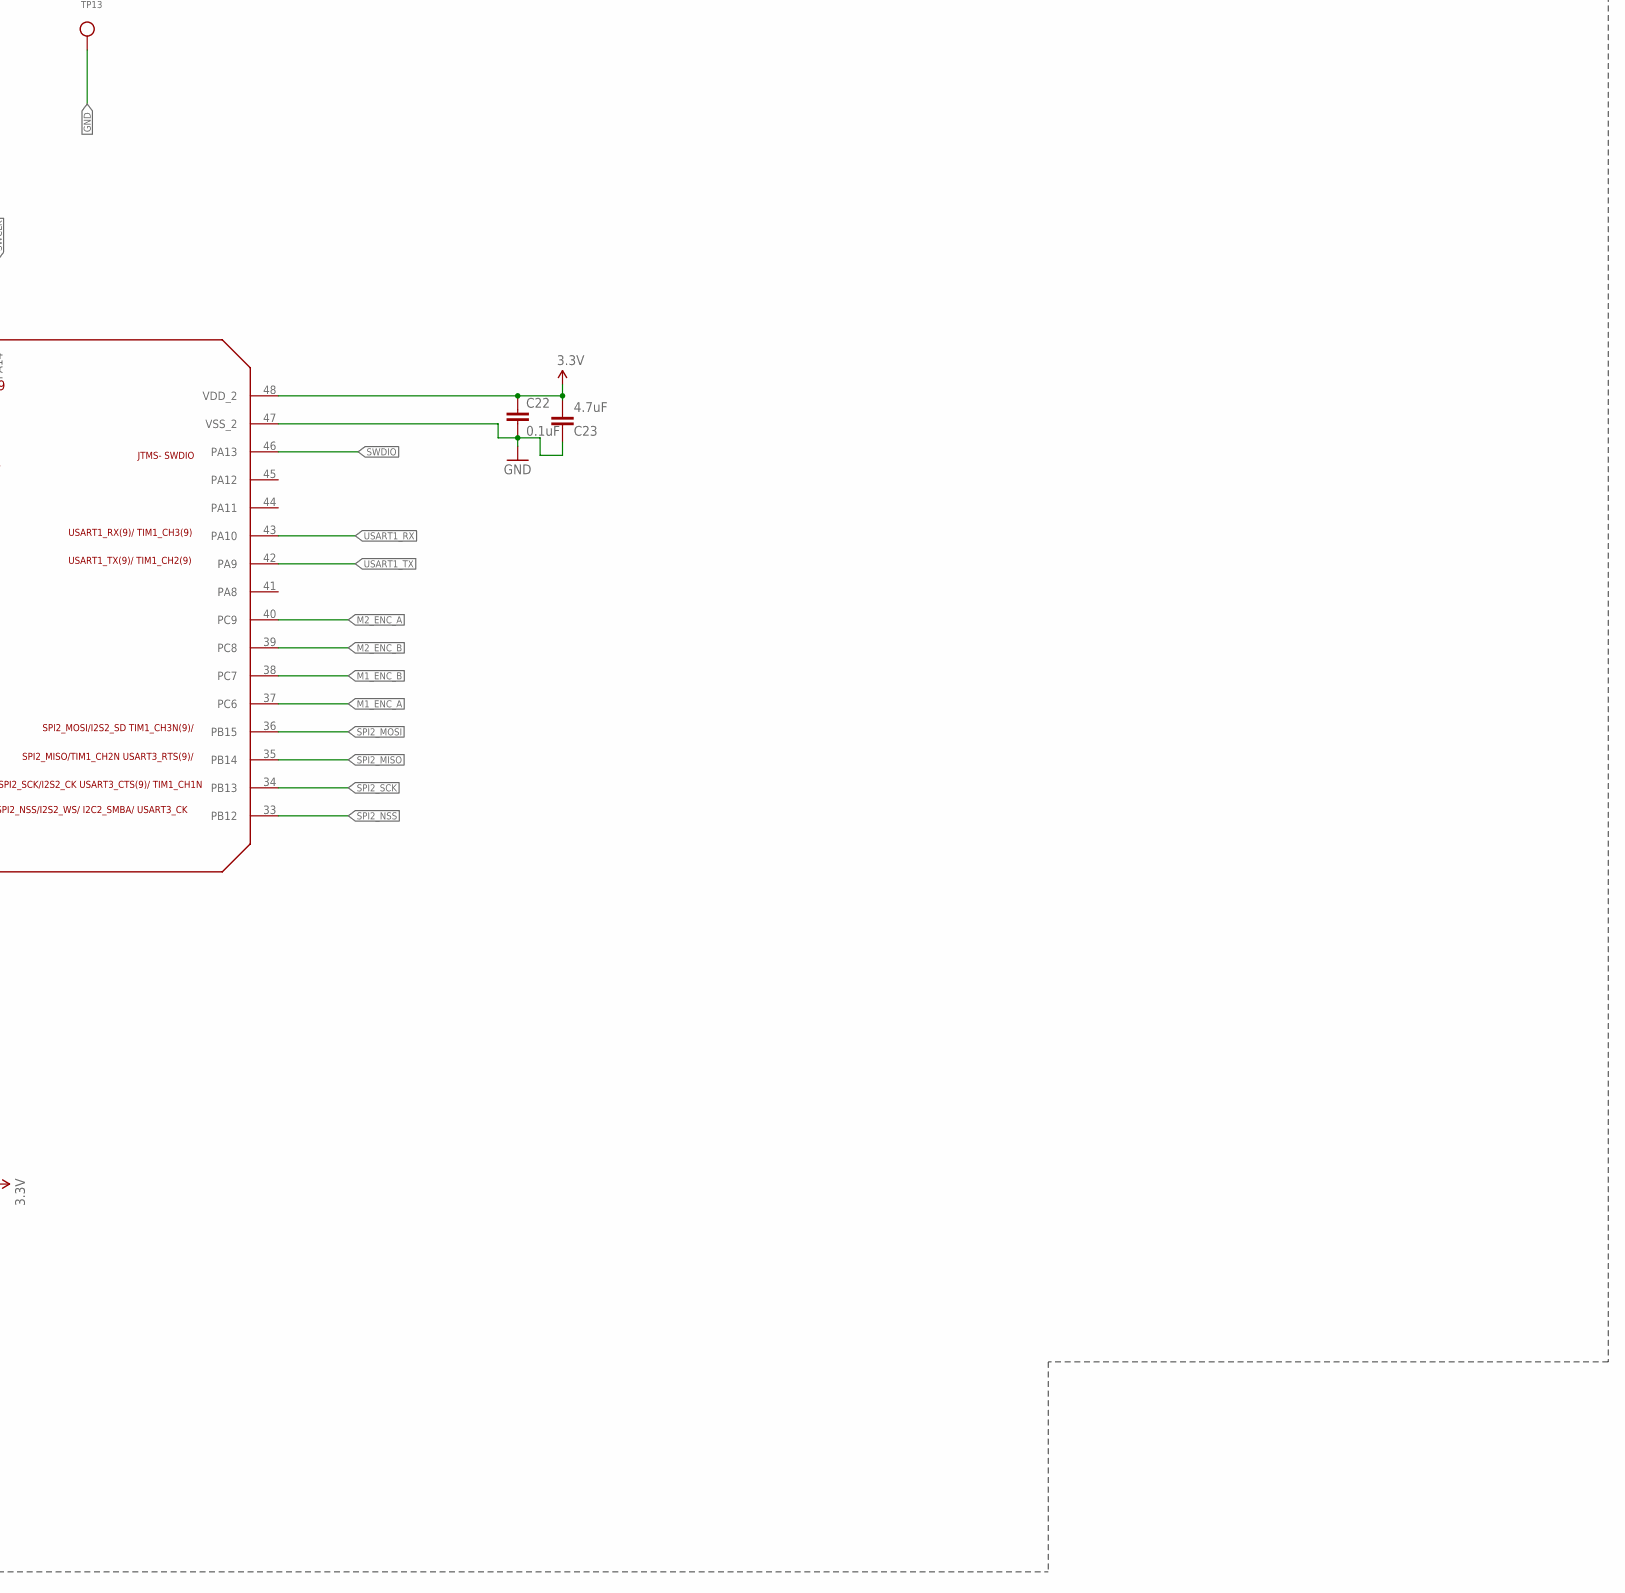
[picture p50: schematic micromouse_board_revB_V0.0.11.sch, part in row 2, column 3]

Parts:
3.3V_PWR, 5V_PWR, 6V_PWR: green; LED-1206
B1, B2, B3: TAC_SWITCHSMD; TACTILE-SWITCH-SMD
C1: 10nF; 0603-CAP
C2, C18, C21, C23: 4.7uF; 0603-CAP
C4, C7, C17, C22: 0.1uF; 0603-CAP
C8: 1uF; 0603-CAP
CR1: STM32F103RET6; LQFP-64
C_3.3V1, C_3.3V6: 10uF; 0603-CAP
C_3.3V2, C_3.3V7, C_5V1: 0.1uF; 0603-CAP
C_3.3V5: 1uF; 0603-CAP
C_5V2: 47uF; 1210
C_BAT1: 0.1uF; 0603-CAP
C_BAT2: 47uF; 1210
C_D: 0.1uF; 0603-CAP
C_D1: 10uF; 0603-CAP
C_D2: 2.2uF; 0603-CAP
C_ELF1: 4.7uF; 0603-CAP
C_ELF2: 0.1uF; 0603-CAP
C_EM_D1: 4.7uF; 0603-CAP
C_EM_D2: 0.1uF; 0603-CAP
C_ERF1: 4.7uF; 0603-CAP
C_ERF2: 0.1uF; 0603-CAP
C_E_H1: 4.7uF; 0603-CAP
C_E_H2: 0.1uF; 0603-CAP
C_NR: 0.1uF; 0603-CAP
C_NRST, C_NRST1, C_NRST2: 0.1uF; 0603-CAP
IMU_C1, IMU_C2: 0.1uF; 0603-CAP
IMU_C3: 2.2nF; 0603-CAP
J1, J4: CONN_04; 1X04
J2, J3: JST_PH; JST_B2B-PH-K-S(LF)(SN)
L1: 10uH; 1007
LEFT_FRONT_EMITTER: EMITTER
NMOS1, NMOS2, NMOS3, NMOS4: DMN3150LW
R4, R5: 4.6k; M0805
REC_LF: RECEIVER
R_B1, R_B2: 47k; 0603-RES
R_ED1, R_ED2: 5.6; 0603-RES
R_ED_PD: 47k; 0603-RES
R_EH1, R_EH2: 5.6; 0603-RES
R_EH_PD: 47k; 0603-RES
R_ELF: 10; 0603-RES
R_ELF_PD: 47k; 0603-RES
R_ERF: 30; 0603-RES
R_ERF_PD: 47k; 0603-RES
R_PWR1, R_PWR3, R_PWR4: 100 Ohm; 0603-RES
R_RLD: 1.8k; 0603-RES
R_RLF: 1.8k; 0603-RES
R_RLH: 1.8k; 0603-RES
R_RRD: 1.8k; 0603-RES
R_RRF: 1.8k; 0603-RES
R_RRH: 1.8k; 0603-RES
R_VM1: 70k; 0603-RES
R_VM2: 40k; 0603-RES
R_VM3, R_VM4: 500m; 0603-RES
R_VM5: 10k; 0603-RES
S2: SWITCH-SPSTPTH; SWITCH-SPDT
T1, T2, T3, T4, T5, T6: TESTPOINTROUND2MM; TESTPOINT_ROUND_2MM
TP7, TP8, TP9, TP10, TP11, TP12, TP13: TESTPOINTROUND2MM; TESTPOINT_ROUND_2MM
U2: DRV8848PWPR; SOP65P640X120-17N
U6: MPU-6000; QFN-24-EP
U$3: TPS73633(SOT-23)
U$4: TPS76850(SOIC-8)
U$5, U$6: 6P_HEADER
U$7, U$8, U$9, U$20, U$21: RECEIVER
U$11, U$13, U$17, U$18, U$19: EMITTER
U$14, U$15: SPARKFUN-SPDT; SPDT
U$16, U$22: SPLITTER
U$23: BD60HC5WEFJ; SOIC127P600X100-9N
X1: RASPI_GPIO_B+#_PIN; RASPI_GPIO_B+_PIN

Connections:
3.3V: C2.2, C4.2, C7.1, C17.1, C18.2, C21.2, C22.1, C23.2, CR1.1 (VBAT), CR1.19 (VDD_4), CR1.32 (VDD_1), CR1.48 (VDD_2), CR1.64 (VDD_3), C_3.3V1.1, C_3.3V2.1, J1.4, J4.2, L1.1, R4.2, R5.2, R_B1.2, R_B2.2, R_PWR4.2, R_VM5.2, U2.1 (NSLEEP), U$3.OUT, X1.1 (3V3A), X1.17 (3V3B)
5V: C_5V1.1, C_5V2.1, C_ELF1.1, C_ELF2.1, C_EM_D1.1, C_EM_D2.1, C_ERF1.1, C_ERF2.1, C_E_H1.1, C_E_H2.1, LEFT_FRONT_EMITTER.+, R_PWR1.2, U$3.EN, U$3.IN, U$4.OUT1, U$4.OUT2, U$11.+, U$13.+, U$18.+, X1.2 (5V0A), X1.4 (5V0B)
6V: C_3.3V5.1, C_D.1, C_D1.1, U2.12 (VM), U$5.3, U$6.3, U$23.1 (VO)
6V_S: R_PWR3.2, U$23.2 (VO_S)
A3.3V: C1.2, C8.2, CR1.13 (VDDA), IMU_C2.1, L1.2, REC_LF.C, U6.13 (VDD), U$7.C, U$8.C, U$9.C, U$20.C, U$21.C
AGND: C1.1, C8.1, CR1.12 (VSSA), IMU_C1.2, IMU_C2.2, IMU_C3.2, R_RLD.1, R_RLF.1, R_RLH.1, R_RRD.1, R_RRF.1, R_RRH.1, R_VM2.1, TP12.P$1, U6.1 (CLKIN), U6.11 (FSYNC), U6.18 (GND), U$22.2
BOOT0: CR1.60 (BOOT0), U$14.P$2
BOOT1: CR1.28 (PB2), U$15.P$2
BRIDGE_A_1: CR1.15 (PA1), U2.16 (AIN1)
BRIDGE_A_2: CR1.16 (PA2), U2.15 (AIN2)
BRIDGE_B_1: CR1.26 (PB0), U2.9 (BIN1)
BRIDGE_B_2: CR1.27 (PB1), U2.10 (BIN2)
D2_EM: R_ED1.2, R_ED2.2, U$17.-
D_EM: U$11.-, U$17.+
EM_D: CR1.59 (PB7), NMOS2.G, R_ED_PD.2
EM_H: CR1.62 (PB9), NMOS4.G, R_EH_PD.2
EM_LF: CR1.58 (PB6), NMOS1.G, R_ELF_PD.2
EM_RF: CR1.61 (PB8), NMOS3.G, R_ERF_PD.2
GND: 3.3V_PWR.C, 5V_PWR.C, 6V_PWR.C, B1.1, B1.2, B2.1, B2.2, B3.1, B3.2, C2.1, C4.1, C7.2, C17.2, C18.1, C21.1, C22.2, C23.1, CR1.18 (VSS_4), CR1.31 (VSS_1), CR1.47 (VSS_2), CR1.63 (VSS_3), C_3.3V1.2, C_3.3V2.2, C_3.3V5.2, C_3.3V6.2, C_3.3V7.2, C_5V1.2, C_5V2.2, C_BAT1.2, C_BAT2.2, C_ELF1.2, C_ELF2.2, C_EM_D1.2, C_EM_D2.2, C_ERF1.2, C_ERF2.2, C_E_H1.2, C_E_H2.2, C_NR.2, C_NRST.2, C_NRST1.2, C_NRST2.2, J1.1, J2.2, J4.1, NMOS1.S, NMOS2.S, NMOS3.S, NMOS4.S, R_ED_PD.1, R_EH_PD.1, R_ELF_PD.1, R_ERF_PD.1, TP13.P$1, U$3.GND, U$4.EN(BAR), U$4.GND, U$14.P$3, U$15.P$3, U$16.1, U$22.1, U$23.3 (GND), U$23.4 (N.C_1), U$23.6 (N.C_2), U$23.7 (N.C_3), U$23.9 (EPAD), X1.6 (GND_A), X1.9 (GND_B), X1.14 (GND_C), X1.20 (GND_D), X1.25 (GND_E), X1.30 (GND_F), X1.34 (GND_G), X1.39 (GND_H)
H2_EM: R_EH1.2, R_EH2.2, U$19.-
H_EM: U$18.-, U$19.+
I2C_SCL: CR1.29 (PB10), R4.1, U6.23 (SCL/SCLK), X1.5 (SCL)
I2C_SDA: CR1.30 (PB11), R5.1, U6.24 (SDA/SDI), X1.3 (SDA)
INT: CR1.56 (PB4), U6.12 (INT)
LF_EM: LEFT_FRONT_EMITTER.-, R_ELF.2
M1_A: U2.2 (AOUT), U$6.1
M1_B: U2.4 (AOUT2), U$6.2
M1_ENC_A: CR1.37 (PC6), TP7.P$1, U$6.4
M1_ENC_B: CR1.38 (PC7), TP8.P$1, U$6.5
M2_A: U2.7 (BOUT1), U$5.1
M2_B: U2.5 (BOUT2), U$5.2
M2_ENC_A: CR1.40 (PC9), TP9.P$1, U$5.4
M2_ENC_B: CR1.39 (PC8), TP10.P$1, U$5.5
MGND: C_D.2, C_D1.2, C_D2.2, R_VM3.2, R_VM4.2, TP11.P$1, U2.13 (GND), U$5.6 (8), U$6.6 (8), U$16.2
unnamed: 3.3V_PWR.A, R_PWR4.1
unnamed: R_VM4.1, U2.3 (AISEN)
unnamed: J2.1, J3.2
unnamed: R_B2.1, U$15.P$1
unnamed: NMOS3.D, R_ERF.1
unnamed: R_B1.1, U$14.P$1
unnamed: NMOS1.D, R_ELF.1
unnamed: R_VM3.1, U2.6 (BISEN)
unnamed: 6V_PWR.A, R_PWR3.1
unnamed: C_D2.1, U2.11 (VREF), U2.14 (VINT)
unnamed: 5V_PWR.A, R_PWR1.1
unnamed: NMOS2.D, R_ED1.1, R_ED2.1
unnamed: NMOS4.D, R_EH1.1, R_EH2.1
unnamed: C_NR.1, U$3.NR/FB
unnamed: IMU_C1.1, U6.10 (REGOUT)
unnamed: IMU_C3.1, U6.20 (CPOUT)
NFAULT: CR1.54 (PD2), R_VM5.1, U2.8 (NFAULT)
PRGM_1: B2.3, B2.4, CR1.10 (PC2), C_NRST1.1
PRGM_2: B3.3, B3.4, CR1.11 (PC3), C_NRST2.1
REC_LD: CR1.23 (PA7), R_RLD.2, T3.P$1, U$7.E
REC_LF: CR1.22 (PA6), REC_LF.E, R_RLF.2, T1.P$1
REC_LH: CR1.8 (PC0), R_RLH.2, T2.P$1, U$21.E
REC_RD: CR1.24 (PC4), R_RRD.2, T4.P$1, U$8.E
REC_RF: CR1.25 (PC5), R_RRF.2, T6.P$1, U$9.E
REC_RH: CR1.9 (PC1), R_RRH.2, T5.P$1, U$20.E
RESET: B1.3, B1.4, CR1.7 (NRST), C_NRST.1
RF_EM: R_ERF.2, U$13.-
SPI2_MISO: CR1.35 (PB14), X1.21 (SPI_MISO)
SPI2_MOSI: CR1.36 (PB15), X1.19 (SPI_MOSI)
SPI2_NSS: CR1.33 (PB12), X1.24 (SPI_CE0)
SPI2_SCK: CR1.34 (PB13), X1.23 (SPI_SCLK)
SWCLK: CR1.49 (PA14), J1.2
SWDIO: CR1.46 (PA13), J1.3
USART1_RX: CR1.43 (PA10), J4.4
USART1_TX: CR1.42 (PA9), J4.3
VBAT_POWER: J3.1, S2.3 (S)
VBAT_SENSE: CR1.17 (PA3), R_VM1.1, R_VM2.2
V_BATT: C_3.3V6.1, C_3.3V7.1, C_BAT1.1, C_BAT2.1, R_VM1.2, S2.2, U$4.IN1, U$4.IN2, U$23.5 (EN), U$23.8 (VCC)

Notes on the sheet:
32 bit MCU Voltage Supply: 2 - 3.5V
PROGRAMMING DEBUG HEADER
Microcontroller
Motor + Encoder
Motor Driver
IR Emitter
IR Receiver
IMU
V_bat = ((40+70)/(40)) * V_mcu V_mcu should not exceed 2.90V
Battery Setup
ADC123_IN0/TIM2_CH1/TIM5_CH1
VINT Ceramic capacitor must be rated for 6.3 V
NSLEEP has internal pulldown
Current Limit = 0.2V/RSENSE Current Limit = 400 mA
AINx, BINx are H bridge.
Use PWM for speed control
PB14/PB15
checked
Power Management
Test points for motors and encoders
C_D2 must be rated to atleast 6.3 V
ADC12_IN8/TIM3_CH3 TIM8_CH3N
USART2_RTS(9) ADC123_IN1/ TIM5_CH2/TIM2_CH2(9)
USART2_TX(9)/TIM5_CH3 ADC123_IN2/ TIM2_CH3 (9)
I2C2_SCL/USART3_TX(9)
I2C2_SDA/USART3_RX(9)
SPI2_NSS/I2S2_WS/ I2C2_SMBA/ USART3_CK
SPI2_SCK/I2S2_CK USART3_CTS(9)/ TIM1_CH1N
SPI2_MISO/TIM1_CH2N USART3_RTS(9)/
SPI2_MOSI/I2S2_SD TIM1_CH3N(9)/
USART1_RX(9)/ TIM1_CH3(9)
USART1_TX(9)/ TIM1_CH2(9)
JTMS- SWDIO
JTCK- SWCLK
PB2/BOOT1
Boot & Reset Switches
Two 3.7V Lipo
Switch to JST PH Connectors
+/-1% output voltage accuracy
C3 needs to be rated for 50 V

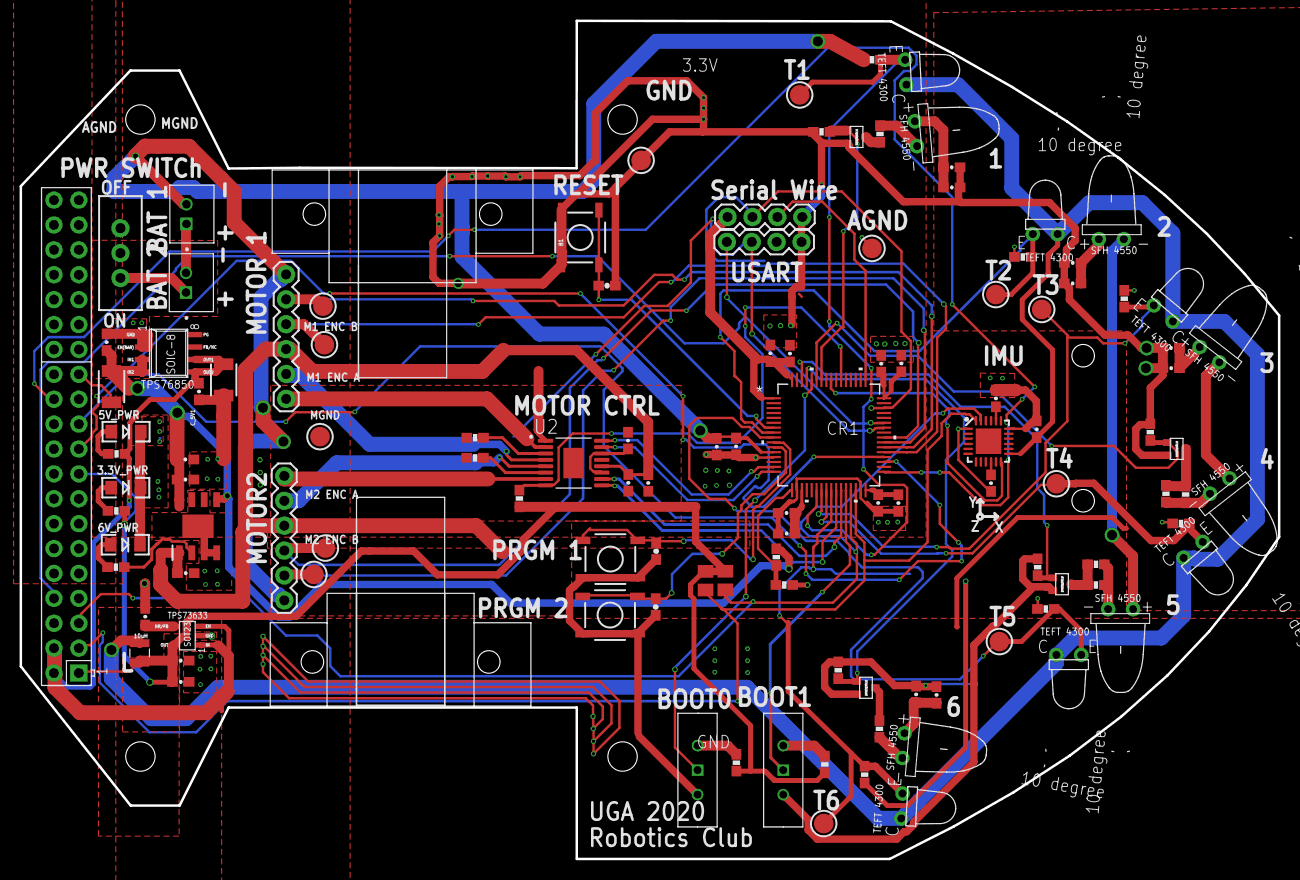
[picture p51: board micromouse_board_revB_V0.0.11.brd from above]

Board: 2 copper layers, 128.4 x 85.5 mm, 119 parts (0 on the bottom side), 72 nets.

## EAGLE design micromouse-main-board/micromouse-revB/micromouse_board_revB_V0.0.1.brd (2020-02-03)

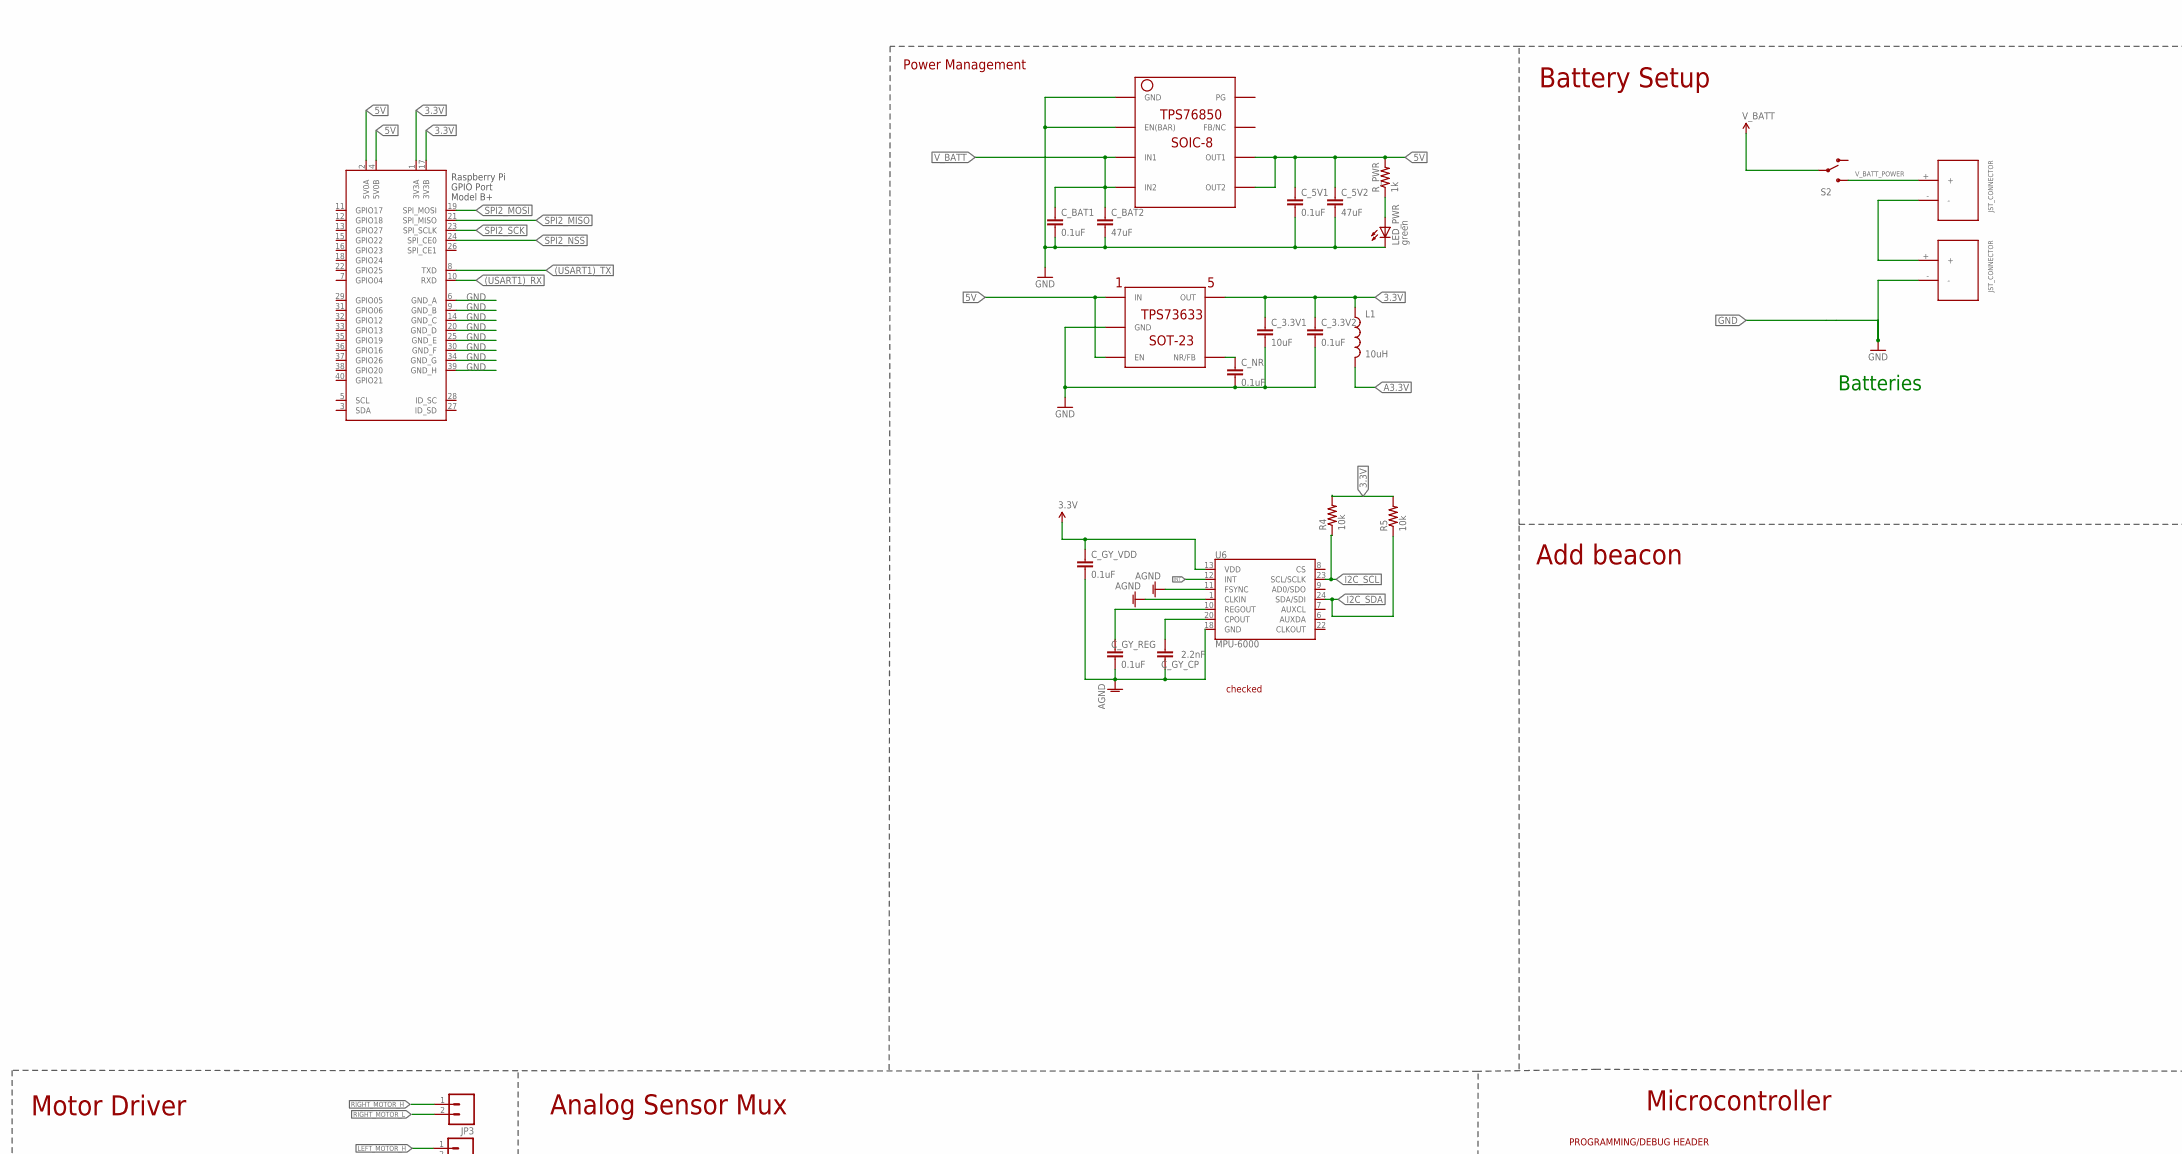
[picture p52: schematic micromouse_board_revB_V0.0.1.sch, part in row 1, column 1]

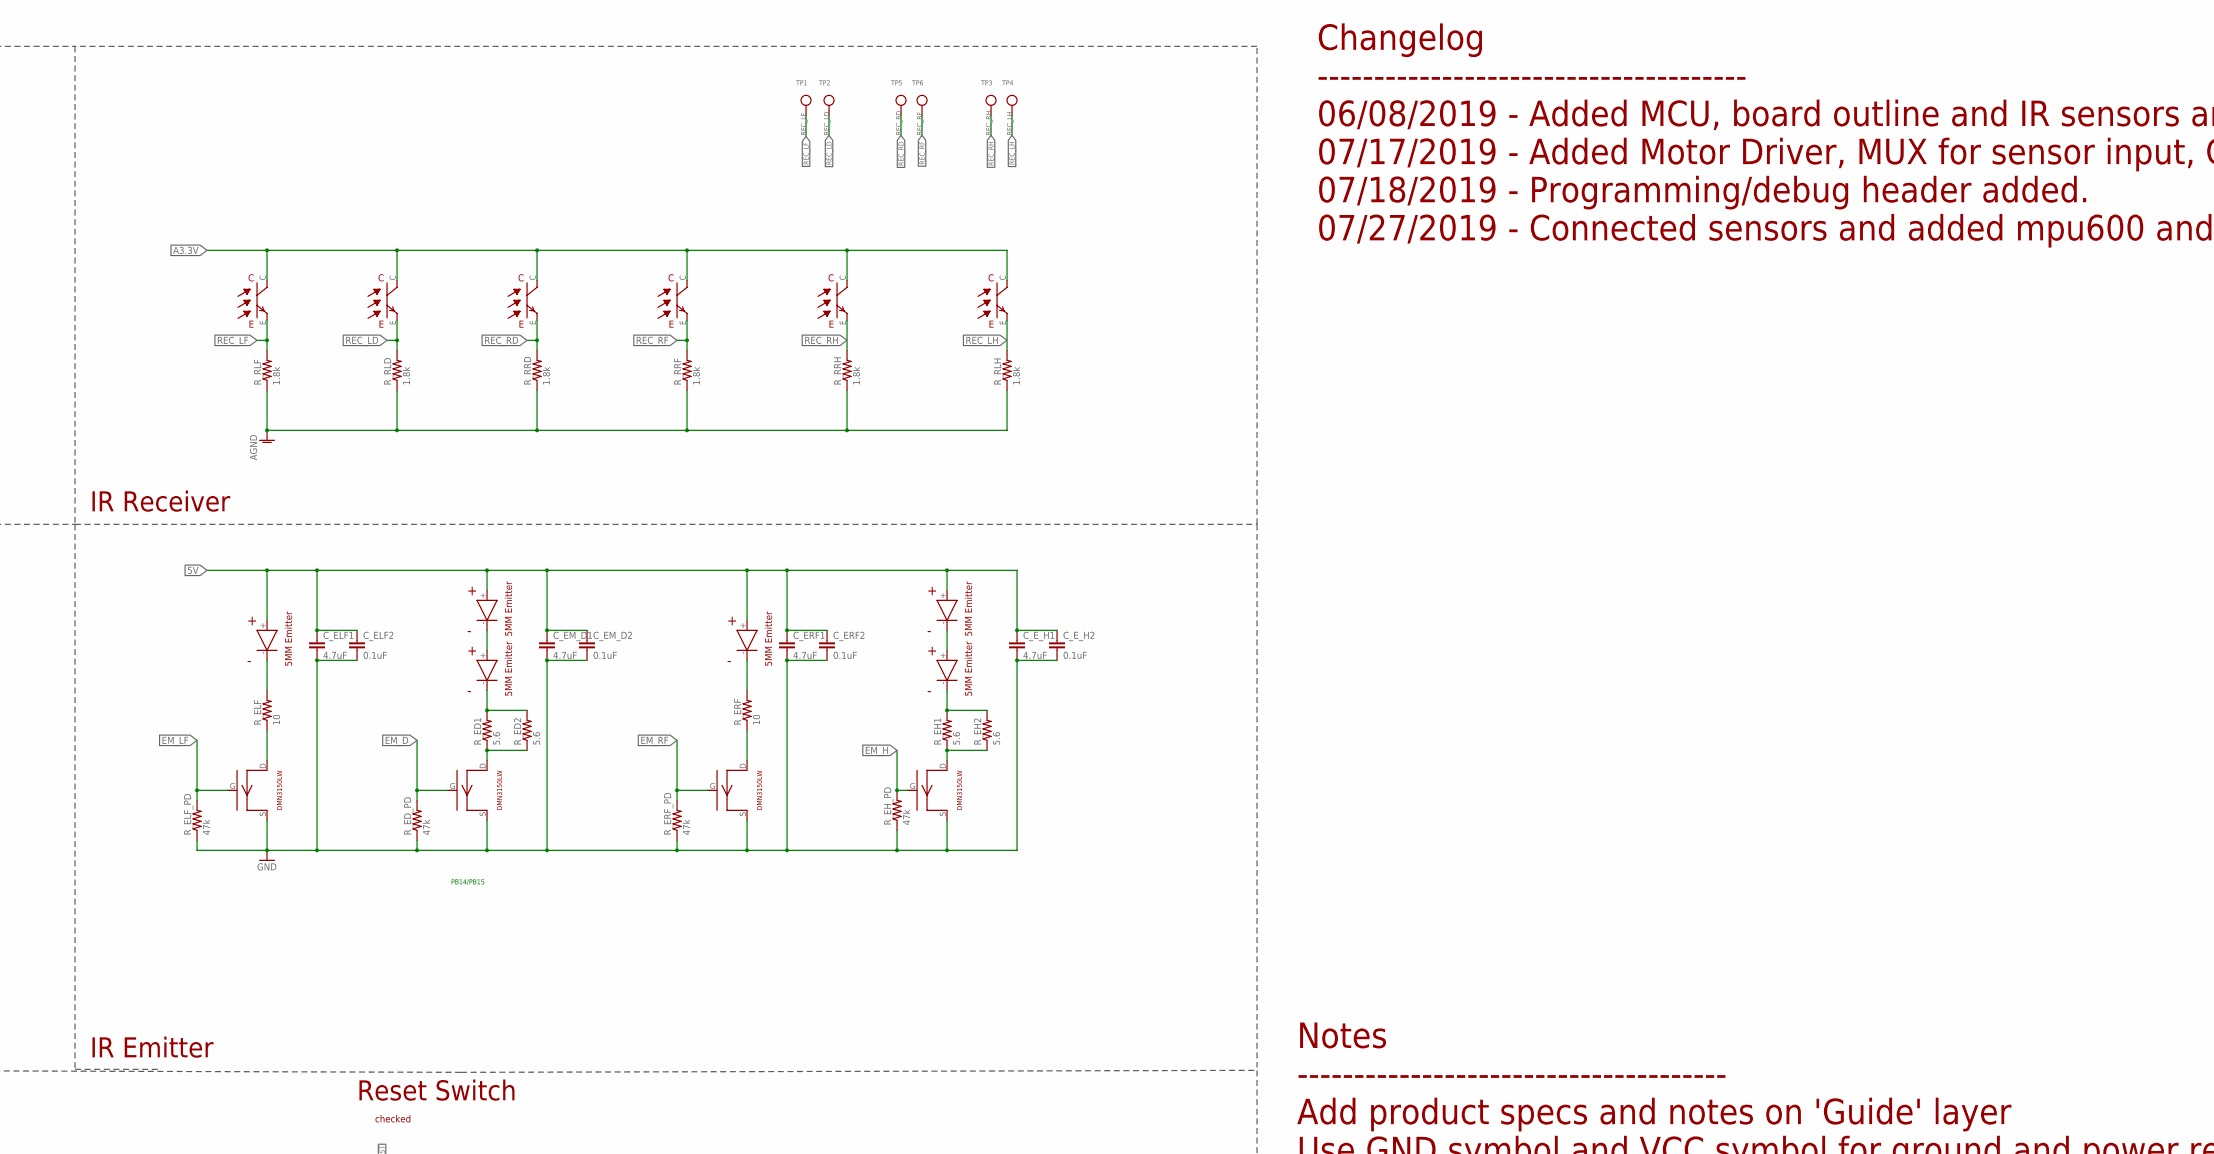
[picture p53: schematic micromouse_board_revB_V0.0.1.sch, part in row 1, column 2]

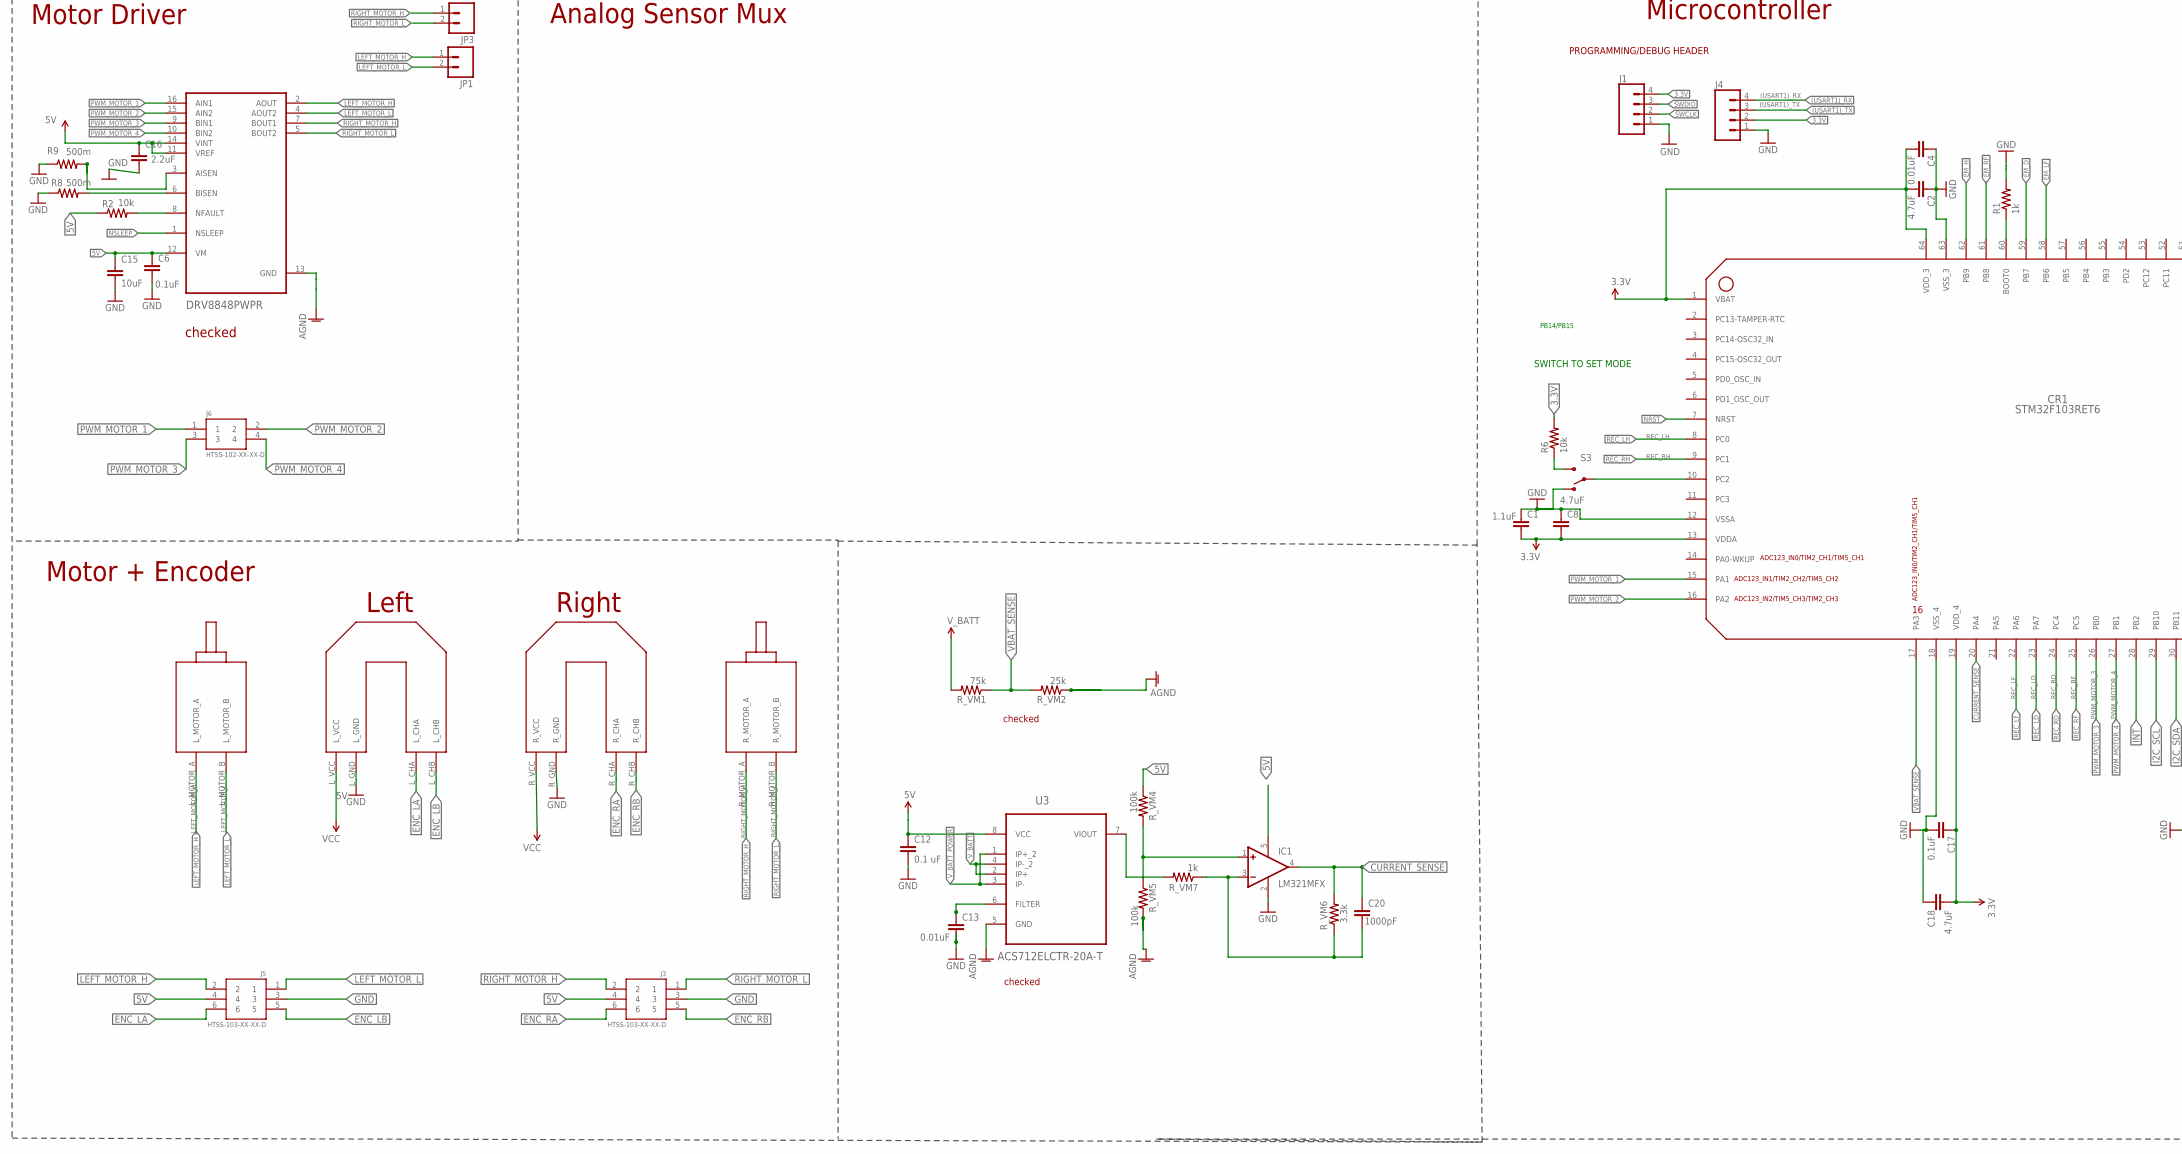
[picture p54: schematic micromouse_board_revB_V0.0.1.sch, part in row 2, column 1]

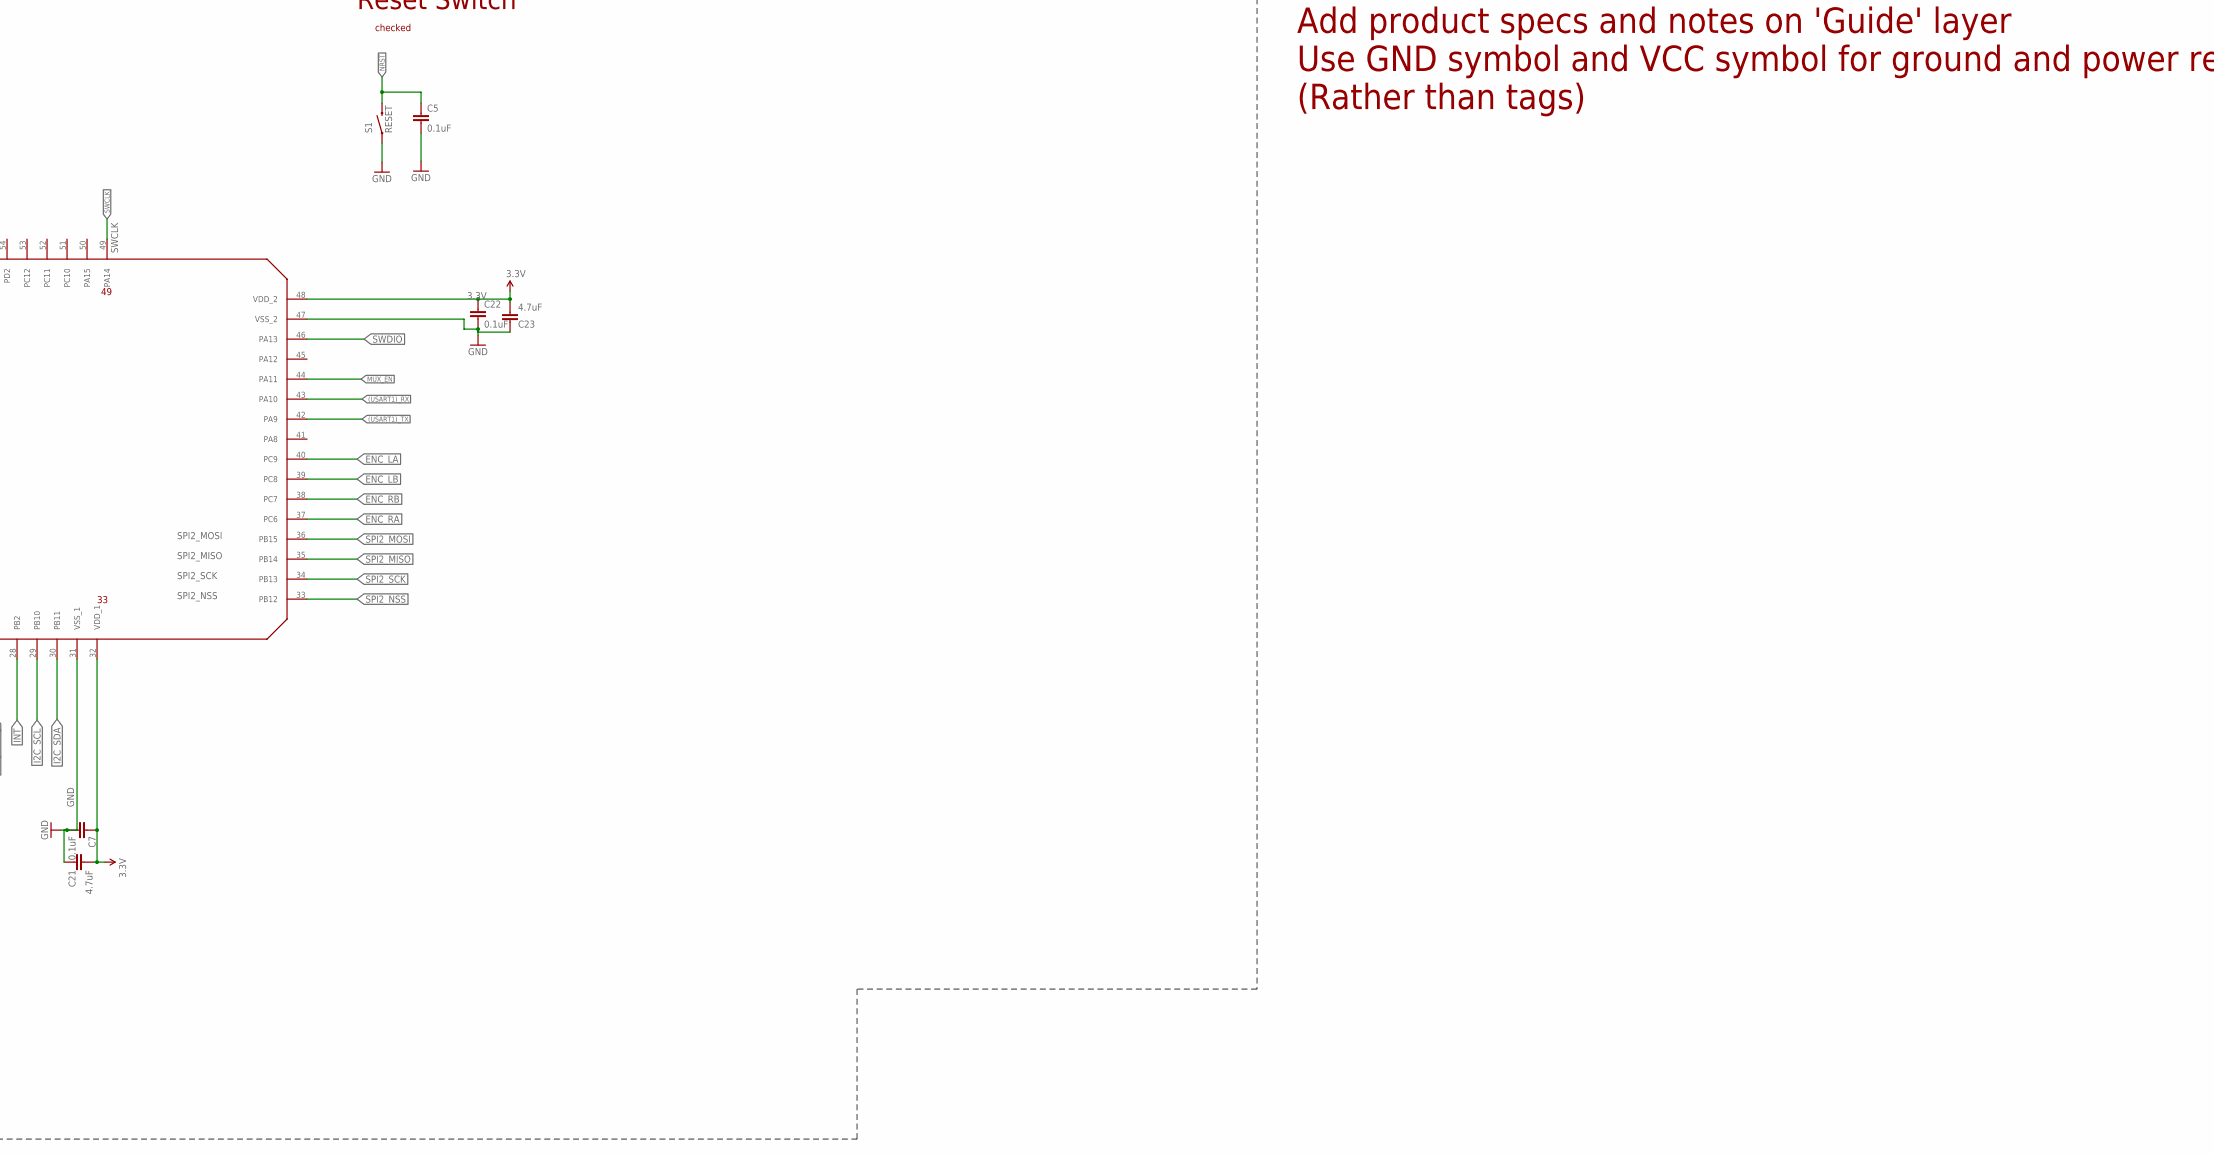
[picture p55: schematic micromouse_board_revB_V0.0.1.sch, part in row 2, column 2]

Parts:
C1: 1.1uF; 0603-CAP
C2, C8, C18, C21, C23: 4.7uF; 0603-CAP
C4, C13: 0.01uF; 0603-CAP
C5, C6, C7, C17, C22: 0.1uF; 0603-CAP
C12: 0.1 uF; 0603-CAP
C15: 10uF; 0603-CAP
C16: 2.2uF; 0603-CAP
C20: 1000pF; 0603-CAP
CR1: STM32F103RET6; LQFP-64
C_3.3V1: 10uF; 0603-CAP
C_3.3V2, C_5V1: 0.1uF; 0603-CAP
C_5V2: 47uF; 1210
C_BAT1: 0.1uF; 0603-CAP
C_BAT2: 47uF; 1210
C_ELF1: 4.7uF; 0603-CAP
C_ELF2: 0.1uF; 0603-CAP
C_EM_D1: 4.7uF; 0603-CAP
C_EM_D2: 0.1uF; 0603-CAP
C_ERF1: 4.7uF; 0603-CAP
C_ERF2: 0.1uF; 0603-CAP
C_E_H1: 4.7uF; 0603-CAP
C_E_H2: 0.1uF; 0603-CAP
C_GY_CP: 2.2nF; 0603-CAP
C_GY_REG: 0.1uF; 0603-CAP
C_GY_VDD: 0.1uF; 0603-CAP
C_NR: 0.1uF; 0603-CAP
IC1: LM321MFX; SOT23-5
J1, J4: CONN_04; 1X04
J3, J5: HTSS-103-XX-XX-D
J6: HTSS-102-XX-XX-D
JP1, JP3: M02POLAR; MOLEX-1X2
L1: 10uH; 1007
LED_PWR: green; LED-1206
LEFT_FRONT_EMITTER: EMITTER
NMOS1, NMOS2, NMOS3, NMOS4: DMN3150LW
R1: 1k; M0805
R2: 10k; 0805
R4, R5, R6: 10k; M0805
R8, R9: 500m; 0805
REC_LF: RECEIVER
R_ED1, R_ED2: 5.6; 0603-RES
R_ED_PD: 47k; 0603-RES
R_EH1, R_EH2: 5.6; 0603-RES
R_EH_PD: 47k; 0603-RES
R_ELF: 10; 0603-RES
R_ELF_PD: 47k; 0603-RES
R_ERF: 10; 0603-RES
R_ERF_PD: 47k; 0603-RES
R_PWR: 1k; 0603-RES
R_RLD: 1.8k; 0603-RES
R_RLF: 1.8k; 0603-RES
R_RLH: 1.8k; 0603-RES
R_RRD: 1.8k; 0603-RES
R_RRF: 1.8k; 0603-RES
R_RRH: 1.8k; 0603-RES
R_VM1: 75k; 0603-RES
R_VM2: 25k; 0603-RES
R_VM4, R_VM5: 100k; 0603-RES
R_VM6: 3.3k; 0603-RES
R_VM7: 1k; 0603-RES
S1: RESET; TACTILE_SWITCH_SMD_4.6X2.8MM
S2, S3: SWITCH-SPSTPTH; SWITCH-SPDT
TP1, TP2, TP3, TP4, TP5, TP6: TESTPOINTROUND2MM; TESTPOINT_ROUND_2MM
U2: DRV8848PWPR; SOP65P640X120-17N
U3: ACS712ELCTR-20A-T; SOIC127P600X175-8N
U6: MPU-6000; QFN-24-EP
U$1, U$2: JST_CONNECTOR_FEMALE
U$3: TPS73633(SOT-23)
U$4: TPS76850(SOIC-8)
U$7, U$8, U$9, U$20, U$21: RECEIVER
U$11, U$13, U$17, U$18, U$19: EMITTER
U$12: MY_MM_MOTOR_MOUNT
X1: RASPI_GPIO_B+#_PIN; RASPI_GPIO_B+_PIN

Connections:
3.3V: C1.2, C2.2, C4.2, C7.1, C8.2, C17.1, C18.2, C21.2, C22.1, C23.2, CR1.1 (VBAT), CR1.13 (VDDA), CR1.19 (VDD_4), CR1.32 (VDD_1), CR1.48 (VDD_2), CR1.64 (VDD_3), C_3.3V1.1, C_3.3V2.1, C_GY_VDD.1, J1.4, J4.2, L1.1, R4.2, R5.2, R6.2, U6.13 (VDD), U$3.OUT, X1.1 (3V3A), X1.17 (3V3B)
5V: C6.1, C12.1, C15.1, C16.1, C_5V1.1, C_5V2.1, C_ELF1.1, C_ELF2.1, C_EM_D1.1, C_EM_D2.1, C_ERF1.1, C_ERF2.1, C_E_H1.1, C_E_H2.1, IC1.5 (V+), J3.4, J5.4, LEFT_FRONT_EMITTER.+, R2.1, R_PWR.2, R_VM4.1, U2.11 (VREF), U2.12 (VM), U2.14 (VINT), U3.8 (VCC), U$3.EN, U$3.IN, U$4.OUT1, U$4.OUT2, U$11.+, U$12.L_VCC, U$12.R_VCC, U$13.+, U$18.+, X1.2 (5V0A), X1.4 (5V0B)
(USART1)_RX: CR1.43 (PA10), J4.4, X1.10 (RXD)
(USART1)_TX: CR1.42 (PA9), J4.3, X1.8 (TXD)
A3.3V: L1.2, REC_LF.C, U$7.C, U$8.C, U$9.C, U$20.C, U$21.C
AGND: C_GY_CP.2, C_GY_REG.2, C_GY_VDD.2, R_RLD.1, R_RLF.1, R_RLH.1, R_RRD.1, R_RRF.1, R_RRH.1, R_VM2.1, R_VM5.2, U2.13 (GND), U3.5 (GND), U6.1 (CLKIN), U6.11 (FSYNC), U6.18 (GND)
BATT_CONN: U$1.+, U$2.-
CURRENT_SENSE: C20.1, CR1.20 (PA4), IC1.4 (OUT), R_VM6.2
D2_EM: R_ED1.2, R_ED2.2, U$17.-
D_EM: U$11.-, U$17.+
EM_D: CR1.59 (PB7), NMOS2.G, R_ED_PD.2
EM_H: CR1.62 (PB9), NMOS4.G, R_EH_PD.2
EM_LF: CR1.58 (PB6), NMOS1.G, R_ELF_PD.2
EM_RF: CR1.61 (PB8), NMOS3.G, R_ERF_PD.2
ENC_LA: CR1.40 (PC9), J5.6, U$12.L_CHA
ENC_LB: CR1.39 (PC8), J5.5, U$12.L_CHB
ENC_RA: CR1.37 (PC6), J3.6, U$12.R_CHA
ENC_RB: CR1.38 (PC7), J3.5, U$12.R_CHB
GND: C1.1, C2.1, C4.1, C5.2, C6.2, C7.2, C8.1, C12.2, C13.2, C15.2, C16.2, C17.2, C18.1, C21.1, C22.2, C23.1, CR1.12 (VSSA), CR1.18 (VSS_4), CR1.31 (VSS_1), CR1.47 (VSS_2), CR1.63 (VSS_3), C_3.3V1.2, C_3.3V2.2, C_5V1.2, C_5V2.2, C_BAT1.2, C_BAT2.2, C_ELF1.2, C_ELF2.2, C_EM_D1.2, C_EM_D2.2, C_ERF1.2, C_ERF2.2, C_E_H1.2, C_E_H2.2, C_NR.2, IC1.2 (V-), J1.1, J3.3, J4.1, J5.3, LED_PWR.C, NMOS1.S, NMOS2.S, NMOS3.S, NMOS4.S, R1.2, R8.1, R9.1, R_ED_PD.1, R_EH_PD.1, R_ELF_PD.1, R_ERF_PD.1, S1.1, S1.2 (1), S3.1 (O), U$1.-, U$3.GND, U$4.EN(BAR), U$4.GND, U$12.L_GND, U$12.R_GND, X1.6 (GND_A), X1.9 (GND_B), X1.14 (GND_C), X1.20 (GND_D), X1.25 (GND_E), X1.30 (GND_F), X1.34 (GND_G), X1.39 (GND_H)
H2_EM: R_EH1.2, R_EH2.2, U$19.-
H_EM: U$18.-, U$19.+
I2C_SCL: CR1.29 (PB10), R4.1, U6.23 (SCL/SCLK)
I2C_SDA: CR1.30 (PB11), R5.1, U6.24 (SDA/SDI)
INT: CR1.28 (PB2), U6.12 (INT)
LEFT_MOTOR_H: J5.2, JP1.1, U2.2 (AOUT), U$12.L_MOTOR_A
LEFT_MOTOR_L: J5.1, JP1.2, U2.4 (AOUT2), U$12.L_MOTOR_B
LF_EM: LEFT_FRONT_EMITTER.-, R_ELF.2
MUX_EN: CR1.44 (PA11)
unnamed: C13.1, U3.6 (FILTER)
unnamed: CR1.10 (PC2), S3.2
unnamed: NMOS3.D, R_ERF.1
unnamed: R6.1, S3.3 (S)
unnamed: NMOS1.D, R_ELF.1
unnamed: CR1.60 (BOOT0), R1.1
unnamed: R2.2, U2.8 (NFAULT)
unnamed: R9.2, U2.3 (AISEN)
unnamed: NMOS2.D, R_ED1.1, R_ED2.1
unnamed: NMOS4.D, R_EH1.1, R_EH2.1
unnamed: R8.2, U2.6 (BISEN)
unnamed: IC1.1 (+IN), R_VM4.2, R_VM5.1
unnamed: R_VM7.2, U3.7 (VIOUT)
unnamed: C_NR.1, U$3.NR/FB
unnamed: LED_PWR.A, R_PWR.1
unnamed: C_GY_REG.1, U6.10 (REGOUT)
unnamed: C_GY_CP.1, U6.20 (CPOUT)
unnamed: C20.2, IC1.3 (-IN), R_VM6.1, R_VM7.1
NRST: C5.1, CR1.7 (NRST), S1.3 (2), S1.4 (2)
NSLEEP: U2.1 (NSLEEP)
PWM_MOTOR_1: CR1.15 (PA1), J6.1, U2.16 (AIN1)
PWM_MOTOR_2: CR1.16 (PA2), J6.2, U2.15 (AIN2)
PWM_MOTOR_3: CR1.26 (PB0), J6.3, U2.9 (BIN1)
PWM_MOTOR_4: CR1.27 (PB1), J6.4, U2.10 (BIN2)
REC_LD: CR1.23 (PA7), R_RLD.2, TP2.P$1, U$7.E
REC_LF: CR1.22 (PA6), REC_LF.E, R_RLF.2, TP1.P$1
REC_LH: CR1.8 (PC0), R_RLH.2, TP4.P$1, U$21.E
REC_RD: CR1.24 (PC4), R_RRD.2, TP5.P$1, U$8.E
REC_RF: CR1.25 (PC5), R_RRF.2, TP6.P$1, U$9.E
REC_RH: CR1.9 (PC1), R_RRH.2, TP3.P$1, U$20.E
RF_EM: R_ERF.2, U$13.-
RIGHT_MOTOR_H: J3.2, JP3.1, U2.7 (BOUT1), U$12.R_MOTOR_A
RIGHT_MOTOR_L: J3.1, JP3.2, U2.5 (BOUT2), U$12.R_MOTOR_B
SPI2_MISO: CR1.35 (PB14), X1.21 (SPI_MISO)
SPI2_MOSI: CR1.36 (PB15), X1.19 (SPI_MOSI)
SPI2_NSS: CR1.33 (PB12), X1.24 (SPI_CE0)
SPI2_SCK: CR1.34 (PB13), X1.23 (SPI_SCLK)
SWCLK: CR1.49 (PA14), J1.2
SWDIO: CR1.46 (PA13), J1.3
VBAT_SENSE: CR1.17 (PA3), R_VM1.1, R_VM2.2
V_BATT: C_BAT1.1, C_BAT2.1, R_VM1.2, S2.2, U3.2 (IP+), U3.4 (IP-_2), U$4.IN1, U$4.IN2
V_BATT_POWER: S2.3 (S), U3.1 (IP+_2), U3.3 (IP-), U$2.+

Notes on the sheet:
Changelog -------------------------------------- 06/08/2019 - Added MCU, board outline and IR sensors and receivers. 07/17/2019 - Added Motor Driver, MUX for sensor input, Current Sensor, picked GPIO to use for MUX select, picked ADC in to route MUX to. 07/18/2019 - Programming/debug header added. 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
Notes -------------------------------------- Add product specs and notes on 'Guide' layer Use GND symbol and VCC symbol for ground and power respectively. (Rather than tags)
PROGRAMMING/DEBUG HEADER
Microcontroller
Reset Switch
Motor + Encoder
Motor Driver
IR Emitter
IR Receiver
Add beacon
Analog Sensor Mux
Batteries
Battery Setup
ADC123_IN0/TIM2_CH1/TIM5_CH1
ADC123_IN1/TIM2_CH2/TIM5_CH2
ADC123_IN2/TIM5_CH3/TIM2_CH3
checked
PB14/PB15
Power Management
SWITCH TO SET MODE

Board: 4 copper layers, 110 parts (0 on the bottom side), 68 nets, no tracks yet.

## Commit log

2019-06-20 Add files via upload
    Build schems from this file. Only includes STM32 processor. Needs power system, motor system, interface for flashing, interface for adding layers, etc.
    [MicroMouseV0.0.1.sch]
2019-06-20 organize file structure
    [MicroMouseV0.0.1.sch]
2019-07-08 added wiki, modified micromouse board layout
    [MicroMouseV0.0.2.brd, MicroMouseV0.0.2.sch]
2019-07-08 got board outline to work
    [MicromouseV0.0.3.brd, MicromouseV0.0.3.sch]
2019-07-09 updated board
    [MicromouseV0.0.3.brd, MicromouseV0.0.3.sch]
2019-07-11 updated BOM
2019-07-12 added mpu dev board
2019-07-18 Added debug header
    [MicromouseV0.0.3.brd, MicromouseV0.0.3.sch]
2019-07-23 added software repo, schematic not complete
    [1717T_SR.igs, 1717T_SR.stp, 1717T_SR.x_t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]
2019-07-31 circuits are there power regulators may need to change, still need to set up the analog power nets
    [MicromouseV0.0.7.brd, MicromouseV0.0.7.sch, MicromouseV0.0.8.brd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]
2019-07-31 eagle schematic was broken, replaced with bckup
    [MicromouseV0.0.7.brd, MicromouseV0.0.8.sch]
2019-08-15 this one works
    [MicromouseV0.0.8.brd, MicromouseV0.0.8.sch]
2019-08-15 changed decoupling caps
    [MicromouseV0.0.9.brd, MicromouseV0.0.9.sch]
2019-08-21 modified ground concept, ran error check
    [MicromouseV01.0.9.brd, MicromouseV01.0.9.sch, MicromouseV1.0.0.brd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]
2019-08-21 gnd concept, and ran error check
2019-08-21 removed weird version name
    [MicromouseV01.0.9.brd, MicromouseV01.0.9.sch]
2019-08-21 added sensor output from mux to generic header. Included RC circuit as well.
    [MicromouseV1.0.1.brd, MicromouseV1.0.1.sch]
2019-09-14 added 3d models for dc motors, updated bom with new encoders and dc motors
    [1516T_SR.igs, 1516T_SR.stp, 1516T_SR.x_t]
2019-09-15 updated bom to reflect motor quotes
2019-10-01 3D board model added to 3D models
    [routed-micromouse-board 1.1.2 v1_CAD.step]
2019-10-02 added bom for edu micromouse
    [micromouse-edu-board-bom.csv, micromouse-edu-board-bom.xlsx]
2019-10-03 added updated bom and changed some board components,these few traces will still need to be routed
    [Micromouse-EDU-Parts.xlsx, micromouse-edu-boardV0.0.1.brd, micromouse-edu-boardV0.0.1.sch]
2019-10-17 edu finalized
    [routed-micromouse-board-2.1.2.brd, routed-micromouse-board-2.1.2.sch]
2019-10-21 finalized micromouse edu with raspi header, includes gerber files
    [micromouse-edu-finalV1.0.0.brd, micromouse-edu-finalV1.0.0.sch]
2019-10-28 added 3d models
    [3224X.stp, AB2_LQFP64_WINGS3D.stl, B2B-PH-K-S(LF)(SN)--3DModel-STEP-56544.STEP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]
2019-11-16 value update to reflect bom
    [micromouse-edu-finalV2.0.0.brd, micromouse-edu-finalV2.0.0.sch]
2020-01-23 Add files via upload
    Added i2c to mpu, added swdio, added switch for changing modes, added ground plane, added agnd plane, routed swdio, changed and routed usart tx and rx.
    [micromouse-boardV1.0.2.brd, micromouse-boardV1.0.2.sch]
2020-01-26 new layout
    [micromouse-boardV1.0.1.brd, micromouse-boardV1.0.1.sch, micromouse-boardV1.0.2.brd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]
2020-02-03 power reg. added placement done
    [micromouse_board_revB_V0.0.1.brd, micromouse_board_revB_V0.0.2.brd, micromouse_board_revB_V0.0.3.brd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]
2020-02-16 planes seem to be layed nicely
    [micromouse_board_revB_V0.0.10.brd, micromouse_board_revB_V0.0.10.sch, micromouse_board_revB_V0.0.4.brd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]
2020-02-19 board finalized
    [micromouse_board_revB_V0.0.10_B.brd, micromouse_board_revB_V0.0.10_B.sch, micromouse_board_revB_V0.0.10_C.brd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]
2020-02-19 added cam processor and gerbers
    [micromouse_board_revB_V0.0.16.brd]
2020-02-21 added complete bom, modified board parts based on part availability
    [Micromouse Materials List-02202020-2.xlsx, micromouse_board_revB_V0.0.16.brd, micromouse_board_revB_V0.0.16.csv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]
2020-10-01 add release bom
    [micromouse_board_revB_V0.0.16.xlsx]

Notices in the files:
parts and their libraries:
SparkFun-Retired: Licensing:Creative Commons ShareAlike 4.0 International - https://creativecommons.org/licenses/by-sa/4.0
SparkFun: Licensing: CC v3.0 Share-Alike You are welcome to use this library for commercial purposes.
